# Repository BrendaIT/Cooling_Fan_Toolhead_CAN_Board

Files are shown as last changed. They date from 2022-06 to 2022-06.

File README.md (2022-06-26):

# Cooling_Fan_Toolhead_CAN_Board
This MOD arises from the need for active cooling on the Toolhead Board CAN for VORON2.4 350 Afterburner with cable chain. When printing ABS or other materials, with the doors closed the Toolhead Board CAN reaches temperatures around 70/80 degrees. In my case the Board went into ERROR_MCU thus stopping the print in progress.
Right here comes the need to implement a fan for Active Cooling on the CAN Board.

I took into account various factors such as:

- Reduced weight in order not to overload the X axis.

- That it was compact in the distance between the motor and the rear part of the Gantry, so as not to touch the Chain.

-That it was efficient to keep the board temperature stable.

- That it was easy to assemble and compatible with the cards on the market:

FLY SHT42, Huvud v0.61, BTT EBB42 CAN v1.0.
STL files are printed in ABS, with 30% fill, 0.20 layer height and internal support.

MATERIAL:

The fan is a Radial 30x30x10mm LINK: https://www.amazon.it/gp/product/B08MKLDGQR/ref=ppx_yo_dt_b_asin_title_o01_s00?ie=UTF8&psc=1
The screws: 2x M3 countersunk head (fixing the support to the motor) 4x M3x20mm (fixing the board to the support) 3x M3x5mm (for fixing the chain)

PRINTING:
-Print the two STL files, bearing in mind that the Fan_Cooling file must be printed with support, as in the photo in the Image folder.

ASSEMBLY:
Step 1: Using the soldering iron, insert the 3 M3 inserts for fixing the chain.

Step 2: Remove the 2 rear / upper screws of the Nema17 motor of the Afterborner, fix the chain holder base with the two screws.

Step 3: Screw in the three screws for securing the chain.

Step 4: Connect all connectors to the card.

Step 5: First insert the fan wires into the hole in the upper left of the Holder, then gently insert the Fan so that the propellers are facing up.

6 Step: Align the board with the four screw holes in the motor mount.

Step 7: Bundle and align the cables so that they do not pinch when tightening the screws, set the fan holder down by aligning the four holes on the top of the board.

Step 8: Screw the four board screws to the motor mount.

9 Step: Connect the fan to a Pin of the Motherboard (you can do it in two ways: 1 connect in parallel to the cooling fan of the hotend on the SHT42, Huvud or EBB Toolboard, in this case we will not need any macro, because the fan will turn on as soon as the hotend fan turns on. 2 insert an extra wire in the cable chain and lead to the printer motherboard, connect to an available PIN, this will be our Negative pole, the positive pole must be taken directly from the connector Power of the Toolboard in this case, we need the macro to set the fan)

Step 10: The Gcode Macro must be inserted in your printer.cfg, remember to change the PIN with your settings, if you have Activated the MCU SHT42 Temperature... 
Comment the session:

 #[temperature_sensor FLY-SHT42]
 
 #sensor_type: temperature_mcu
 
 #sensor_mcu: sht42

and add the new macro which already includes the MCU temperature reading.

 # Printer.cfg

[temperature_fan sht42_cool]

pin: PD14 # Bed Heater terminals, XYE board

max_power: 1.0

max_speed: 1.0

min_speed: 0.05

shutdown_speed: 0.0 # 0.9

kick_start_time: 0.1

cycle_time: 0.01 # 0.01

off_below: 0.25 # 0.15

sensor_type: temperature_mcu

sensor_mcu: sht42

#sensor_pin: PF4 # TH0 socket, Z board

min_temp: 0

max_temp: 80

target_temp: 50.0

control: pid

hardware_pwm: false

pid_kp: 40.0

pid_ki: 5.0

pid_kd: 0.01

#gcode_id: A

The game is done! If the temperature of the Toolboard goes above 50.0 degrees the fan turns on thus keeping the card not above 50.0 and consequently avoiding errors.

Good Printing!

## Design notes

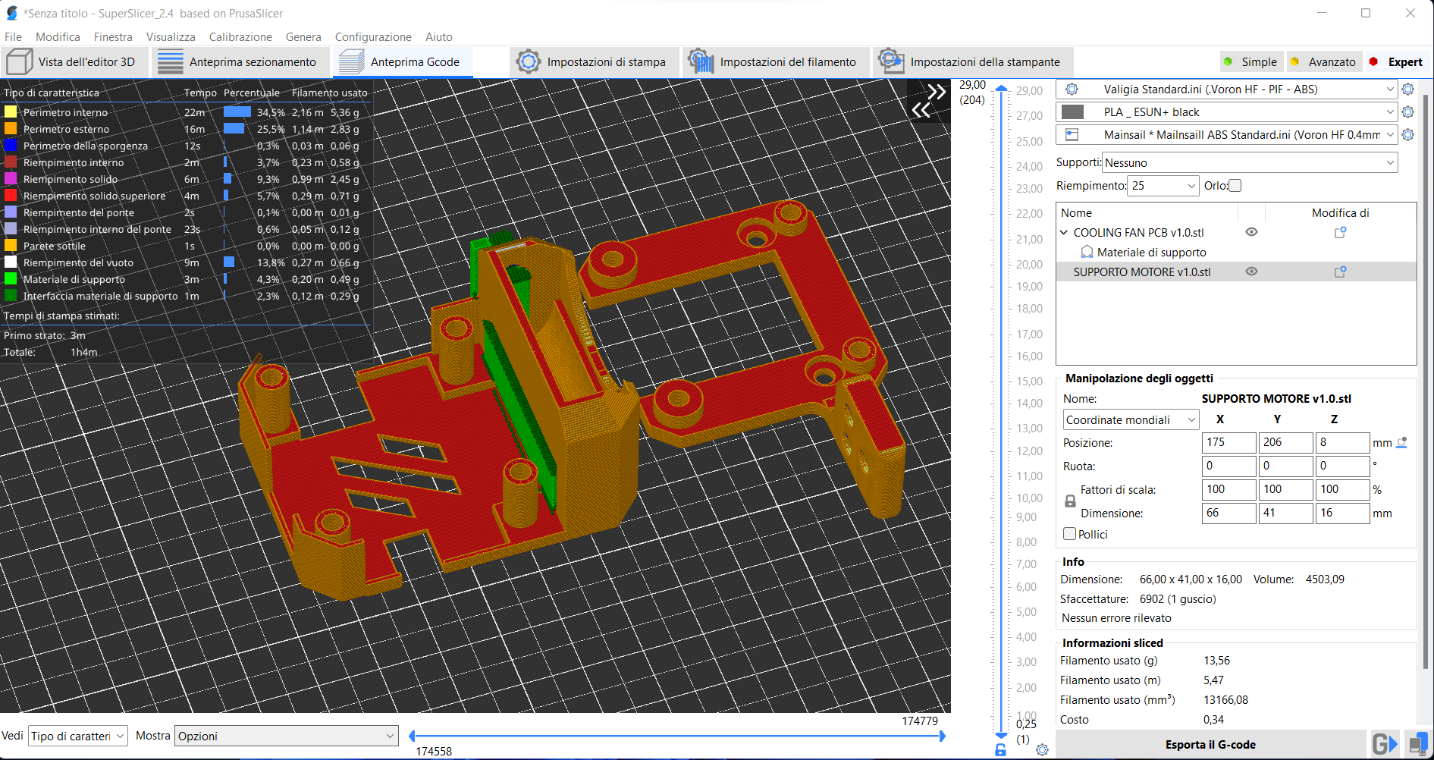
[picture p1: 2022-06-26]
Image/imag_5.png

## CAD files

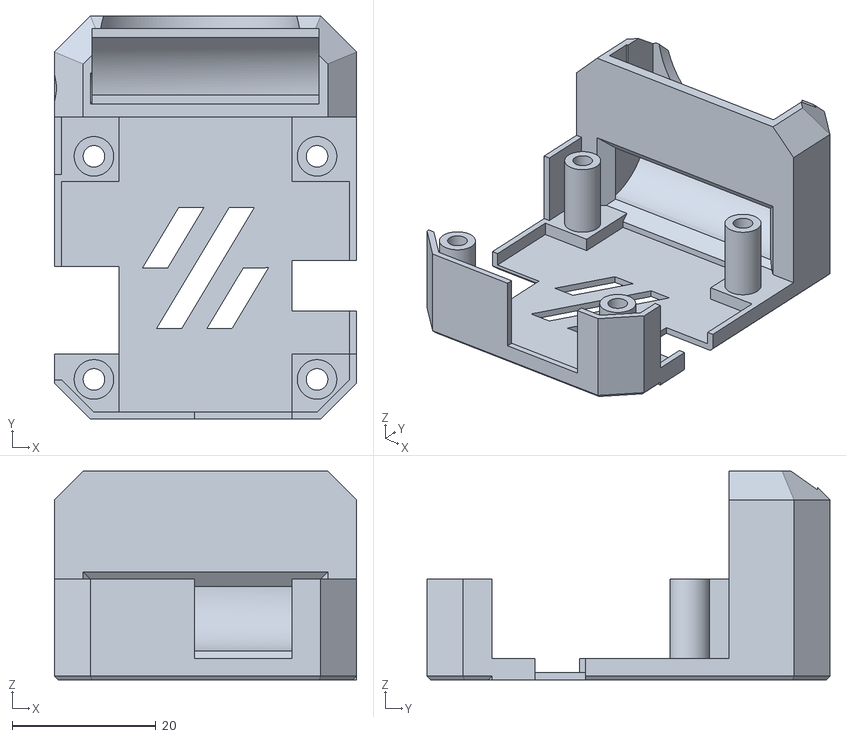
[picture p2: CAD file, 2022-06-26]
STL/Cooling_Fan_ v1.0.stl
42.0 x 56.0 x 29.0

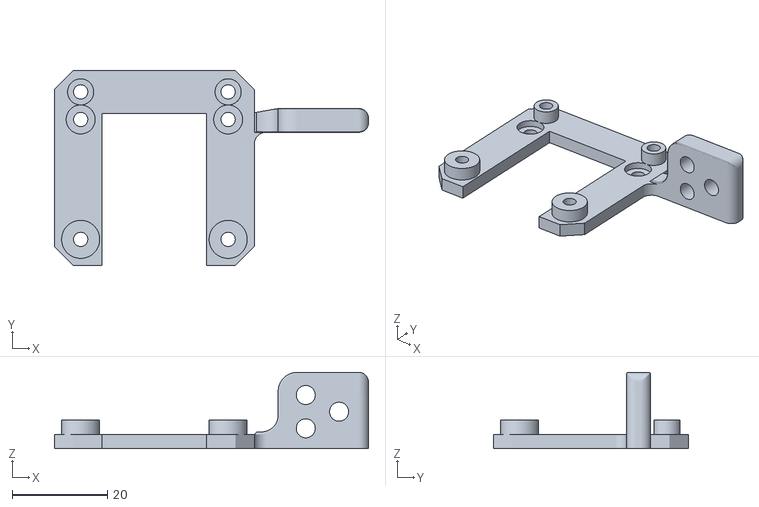
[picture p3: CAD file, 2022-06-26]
STL/Chain_support_v1.0.stl
66.0 x 41.0 x 16.0
